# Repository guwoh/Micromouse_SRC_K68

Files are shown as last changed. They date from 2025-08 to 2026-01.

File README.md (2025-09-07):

# Micromouse_SRC_K68
# Welcome

BOM list: https://docs.google.com/spreadsheets/d/1yc7NAcJtB-HrwJn92QKEUpOmXSOkb5Ers7y2r0_20j4/edit?usp=sharing

//////////

Khung xe:

Tham khảo 1 http://greenye.net/Pages/Micromouse/Futura.htm Tham khảo 2 https://github.com/ukmars/ukmarsbot Tham khảo 3 https://contest.techbriefs.com/2023/entries/robotics-and-automation/12536 Tham khảo 4 https://kswichit.net/micromouse/micromouse.html

/////////////////

VL53l0x lazer sensor connection: https://copilot.microsoft.com/sl/jY64h9Ku57s https://github.com/pololu/vl53l0x-arduino https://learn.adafruit.com/adafruit-vl53l0x-micro-lidar-distance-sensor-breakout/arduino-code

////////////////

Motor driver https://learn.adafruit.com/adafruit-drv8833-dc-stepper-motor-driver-breakout-board/overview

//////////

MPU6050 https://microcontrollerslab.com/micropython-mpu-6050-esp32-esp8266/ http://community.heltec.cn/t/problem-using-mpu-6050-accel-gyro-with-wifikit-esp32-board/2227/8

ESP32 pinout: https://lastminuteengineers.com/handling-esp32-gpio-interrupts-tutorial/ https://lastminuteengineers.com/esp32-pinout-reference/

Kalman Filter: https://www.kalmanfilter.net/alphabeta.html

test merge

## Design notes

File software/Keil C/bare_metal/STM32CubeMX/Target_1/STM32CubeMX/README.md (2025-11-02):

1. 📚 Phần khai báo (Ở đầu file)
/* USER CODE BEGIN Includes */

Chức năng: Nơi để bạn thêm các lệnh #include của riêng mình.

Ví dụ: #include "my_gpio_driver.h"

/* USER CODE BEGIN PTD */ (Private TypeDef)

Chức năng: Nơi để định nghĩa các typedef (struct, enum) của riêng bạn.

Ví dụ: typedef struct { ... } SensorData_t;

/* USER CODE BEGIN PD */ (Private Define)

Chức năng: Nơi để thêm các lệnh #define hằng số.

Ví dụ: #define LED_PIN 5

/* USER CODE BEGIN PV */ (Private Variables)

Chức năng: Nơi để khai báo các biến toàn cục (global variables).

Ví dụ: uint32_t g_tick_count = 0;

/* USER CODE BEGIN PFP */ (Private Function Prototypes)

Chức năng: Nơi khai báo "prototype" (nguyên mẫu hàm) cho các hàm bạn tự viết.

Ví dụ: void My_Clock_Init(void);

/* USER CODE BEGIN 0 */

Chức năng: Nơi để viết các hàm (ví dụ: hàm xử lý ngắt SysTick_Handler) trước hàm main().

2. ⚙️ Bên trong hàm main()
/* USER CODE BEGIN 1 */

Chức năng: Nơi để code chạy ngay khi vào main().

Vị trí VÀNG cho code bare-metal: Đây là nơi hoàn hảo để bạn đặt hàm khởi tạo clock (RCC) của mình.

/* USER CODE BEGIN Init */ & /* USER CODE BEGIN SysInit */

Chức năng: Dùng để khởi tạo các thành phần hệ thống khác. Bạn có thể đặt hàm khởi tạo Systick của mình ở đây.

/* USER CODE BEGIN 2 */

Chức năng: Nơi để code khởi tạo trước vòng lặp while(1).

Vị trí VÀNG cho code bare-metal: Đây là nơi hoàn hảo để bạn đặt hàm khởi tạo ngoại vi (GPIO, UART, Timers...) sau khi clock đã chạy ổn định.

/* USER CODE BEGIN 3 */

Chức năng: Nơi chứa code logic chính của bạn.

Vị trí VÀNG cho code bare-metal: Code của bạn trong vòng lặp while(1) sẽ được đặt ở đây.

3. 📝 Phần định nghĩa hàm (Ở cuối file)
/* USER CODE BEGIN 4 */

Chức năng: Nơi để viết nội dung/định nghĩa cho các hàm mà bạn đã khai báo ở PFP.

Ví dụ:

C

void My_Clock_Init(void)
{
  // Code RCC bare-metal của bạn
}

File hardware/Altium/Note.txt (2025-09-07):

- dong co se duoc lam cao len 2mm
- tìm mt6701 và do chan nam cham, ròi v3 3d
- phần 3d nam châm làm sau

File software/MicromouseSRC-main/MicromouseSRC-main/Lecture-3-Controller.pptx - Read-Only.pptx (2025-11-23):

## Lecture 3: The Controller

PID Control and Speed Profile

## Objective (to be completed over the next 2-3 weeks)

- Create a system that allows you to easily control the angular and translational velocity of your mouse
- Utilize feedback from multiple sensors (IR sensors, encoders, gyro)
- Mouse should accelerate and decelerate at a constant rate, for both angular and translational movement
- Mouse should not collide with walls
- Control your mouse using practical measurement units, like millimeters

## Overview

- Most of the code will be in the systick handler
  - This will make sure that your mouse is always maintaining the correct velocity
  - Also makes sure we can obtain accurate velocities, since we know the time between systick calls (1 ms).
- From outside your controller, you will be able to set the mouse’s two velocities (angular and translational). The controller will automatically accelerate or decelerate to that velocity, then maintain it.

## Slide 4

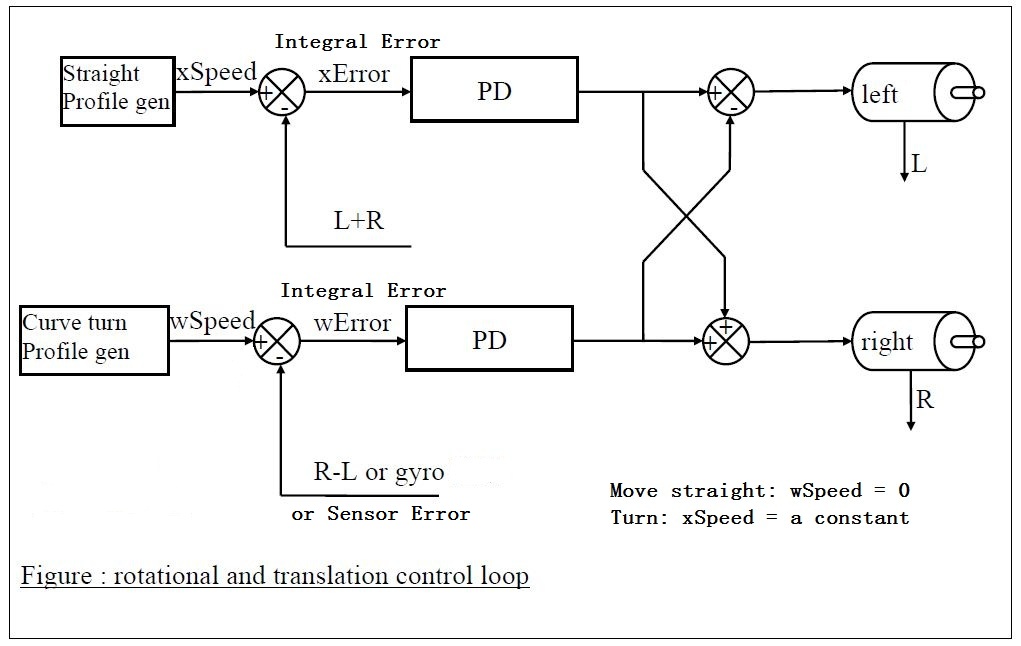
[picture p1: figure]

## Speed Profile

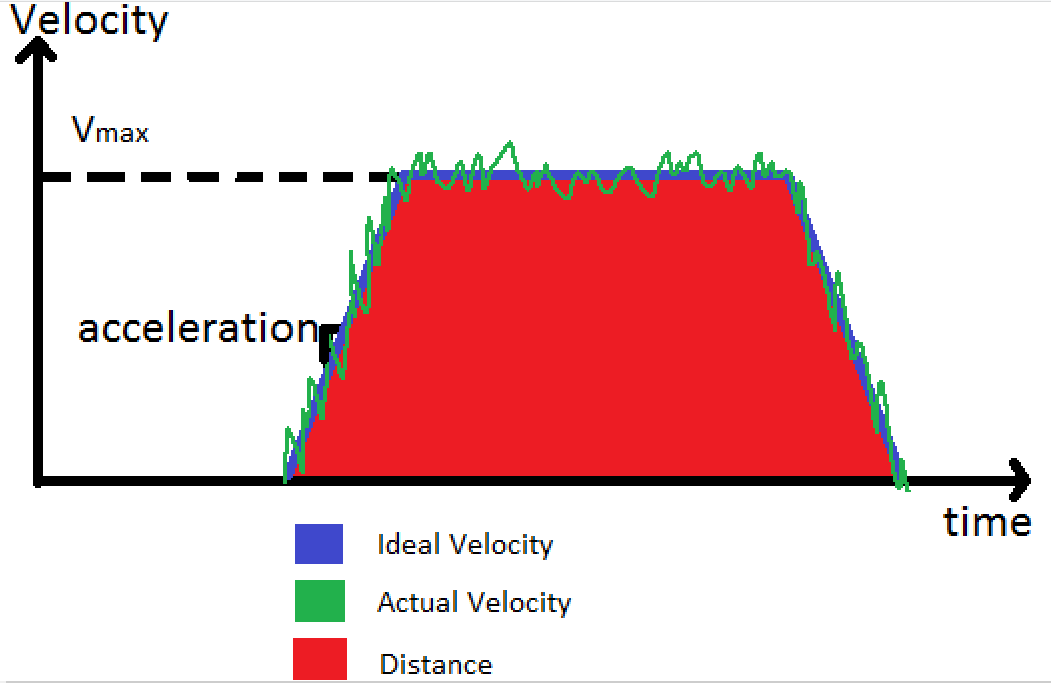
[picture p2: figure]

## The Steps

Within 1ms we need to finish all things as follow in sequence
1. Collect data from all Sensors(IR, gyro, encoders)
2. Decide the ideal velocities you want
3. Find the actual velocities from sensors as feedback(encoder value for translational velocity and gyro for rotational velocity)
4. Find difference between ideal velocity and feedback as Error
5. Input errors to PD controller in a clever way
6. Set the PWM of the motors based on the output from PD controller

## Find the actual velocities

- Take the derivative of the encoder counts
- Gyro also gives you the angular velocity

## Find the ideal velocities

- If you are accelerating or decelerating, then add or subtract (respectively) your acceleration rate from the previous ideal velocity to get the current ideal velocity
- If you are not accelerating or decelerating, then your current ideal velocity is unchanged
- This creates the ideal trapezoidal shape for your speed profile

## Get the PID input

- For translational:
  - We really only have encoders for feedback, since the gyro doesn’t tell us translational movement and the front sensors don’t have a wall close enough most of the time
  - Therefore we can use the ideal velocity minus the actual velocity for our PID input
- For angular:
  - Same as the translational, but we can add sensor error and gyro error.
    - You will need to scale the gyro output so that has roughly the same value as the encoder error
    - Note that the sensor error is a positional error, while the encoder and gyro errors are velocities

## Apply PID to errors

- The velocity error is already your D (remember we took the derivative of the encoder count at the beginning)
- Integrate the velocity error to obtain P.
- Essentially what we want is a “Positional PD Controller”.
- However, we also want to use PI for our sensor error.
  - Integrating the sensor error allows us to permanently correct our angle if the angle of our mouse is off.
- Using a PI controller for our encoder velocity error, gyro error, and (positional) sensor error will give us everything we want.

## Set the PWM of the motors

- Something like this should be at the end of your systick function:
setLeftPwm(errorX – errorW);
setRightPwm(errorX + errorW);
- errorX is the translational error
- errorW is the angular error
- You can change the direction of errorW if you want, just switch the + and -

## Get sensor error

if(DLSensor > DLMiddleValue && DRSensor < DRMiddleValue)
sensorError = DLMiddleValue - DLSensor;
else if(DRSensor > DRMiddleValue && DLSensor < DLMiddleValue)
sensorError = DRSensor - DRMiddleValue;
else
sensorError = 0;

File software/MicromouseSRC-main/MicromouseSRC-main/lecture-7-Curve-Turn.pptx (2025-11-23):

## Lecture 7 Curve Turn

## Basic Concepts

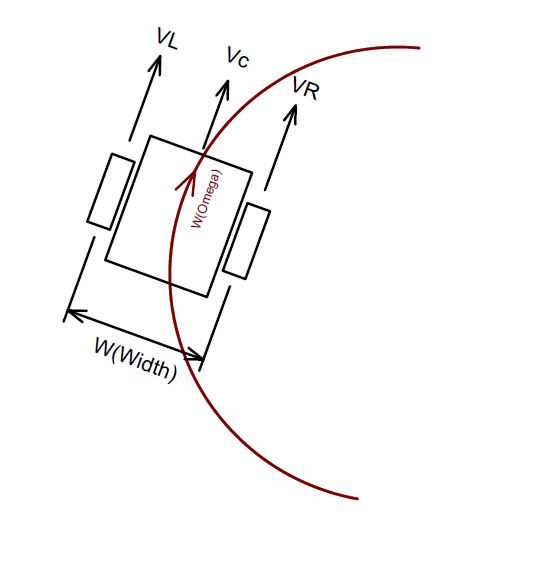
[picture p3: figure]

- Keep speed with certain ratio between 2 wheels for mouse to make mouse turn at certain angular velocity
- However this is not possible in real word
- When on straight, VLs=VRs
- When turn VLt>VRt
- Motor can’t suddenly change speed from VLs to VLt, and VRs to VRt

## Diagram view

This is not possible in real world!

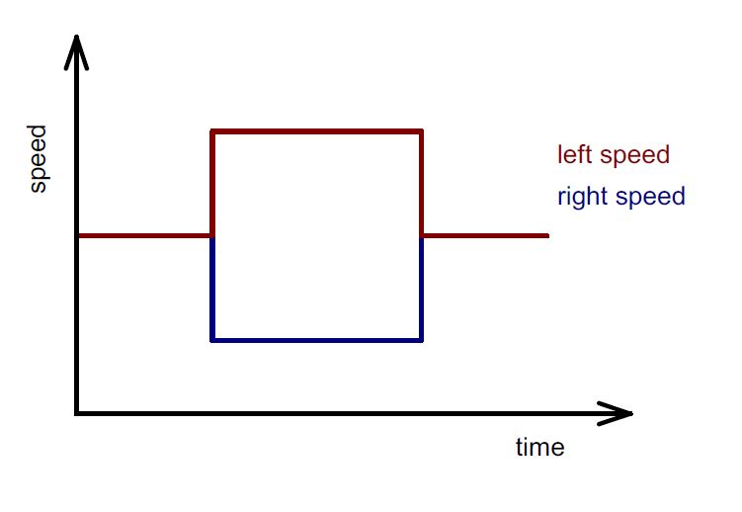
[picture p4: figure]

## Alternative solution

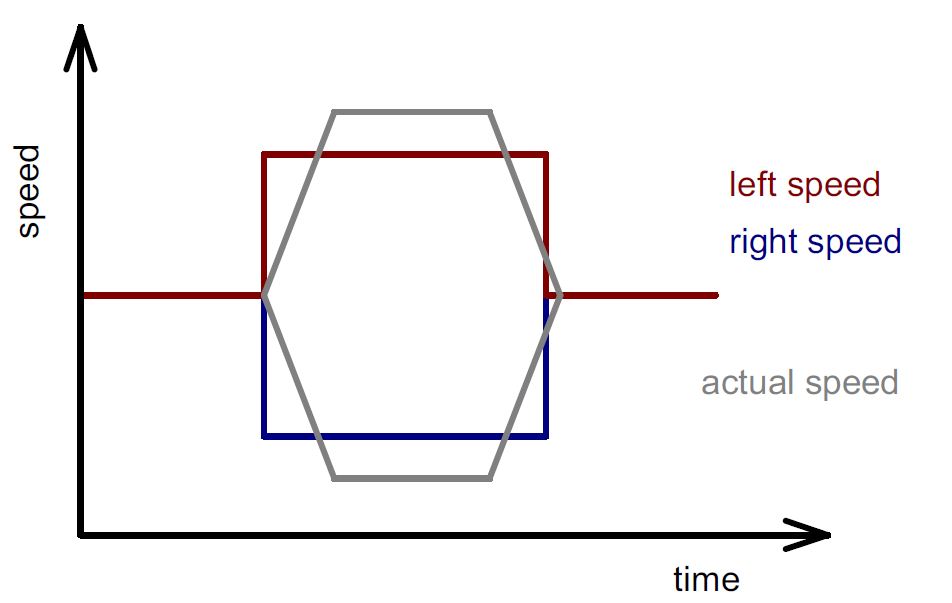
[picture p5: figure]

Make one wheel accelerate, the other wheel decelerate to reach different speed gradually

## How to maintain same turn angle in this way?

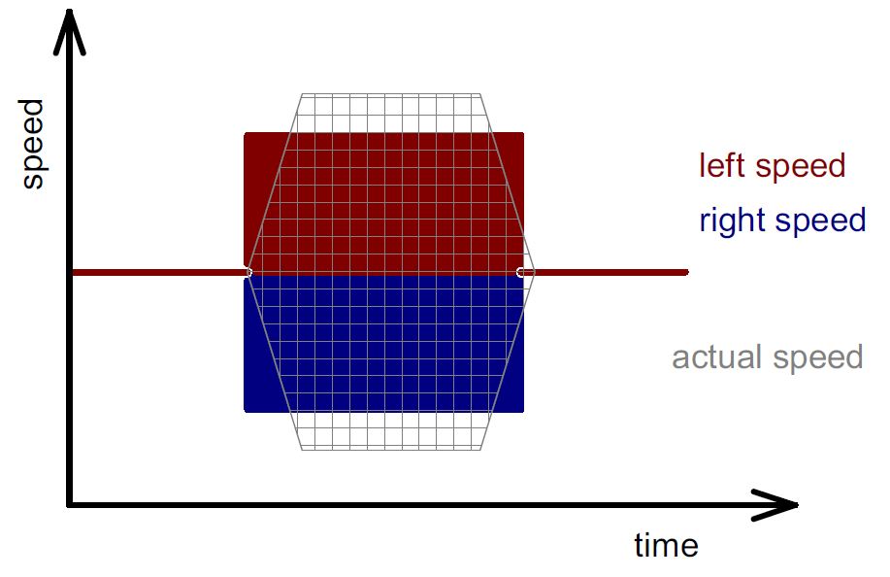
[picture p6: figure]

- All you need to do is just to keep the grey area equals to the sum of red and blue area to maintain the same turning angle

## Some facts

- The center speed of mouse remains constant when turning since VC = (VL + VR)/2
- VR – VL is still the rotational feedback when turning
- You can use the feedback from gyro to replace VR-VL to prevent slippage, however needs to be scale to fit the system with encoder ticks

## The view of angular velocity

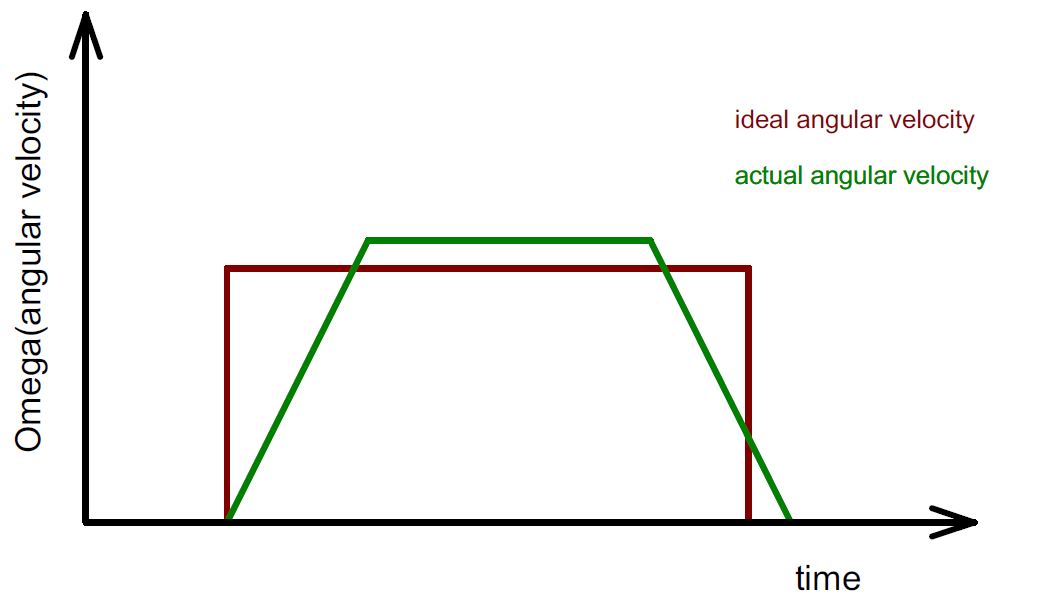
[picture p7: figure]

- W(omega) = VR – VL in our system
- Diagram in angular velocity form is more straight forward since the center linear velocity of mouse doesn’t change during the turn

## Keep the area same

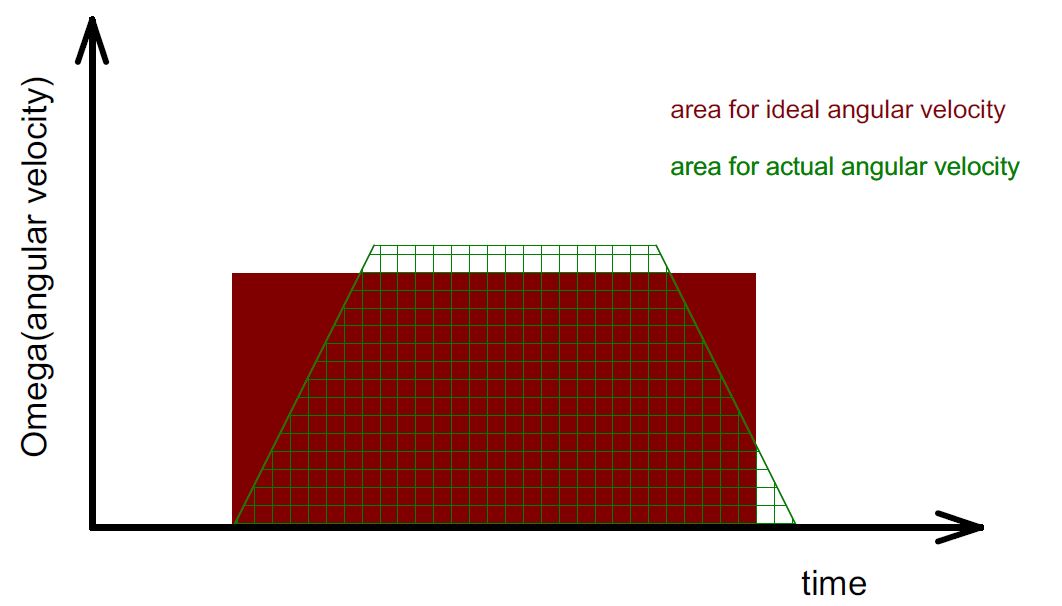
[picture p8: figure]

- As long you keep the area same between ideal and actual angular velocity, the mouse will turn with same angle you desired
- Some extra time is usually needed for actual turn

## How to design your profile?

- Decide the max angular velocity W(omega)
- Decide the angular acceleration (alpha)
- Calculate the area for idea turn, make the actual turn area equals to it
- Use matlab, excel to make your profile, and keep track of the position of the mouse at each millisecond, keep adjusting the input parameters, until the actual output curve for mouse exits at same location with idea curve
- Apply the parameter decided from simulation profile to your mouse

## An example with excel

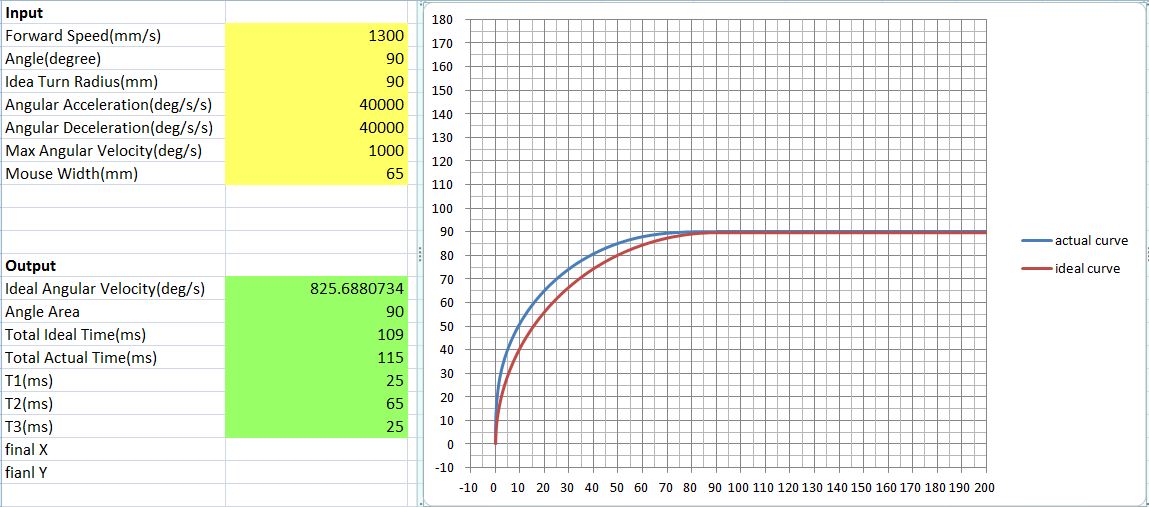
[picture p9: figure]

## Demo with the simulation profile

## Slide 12

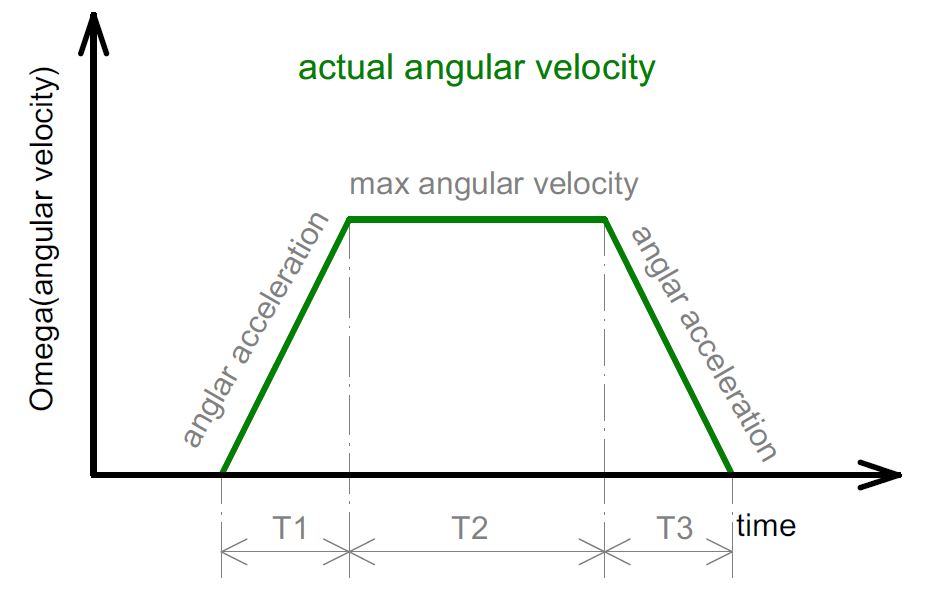
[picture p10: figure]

## How to make it work on mouse?

- Center forward linear velocity, turn angle, angular acceleration, max angular velocity are all know in this case.
- Assume T1 = T3 to simplify the case where the slope(angular acceleration rate) are same
- Calculate the corresponding angular velocity with T1, slope or max angular velocity at T1 and T3
- The angular velocity is max angular velocity at T2

## Sample code

- Having this is your controller:
- If currentSpeedW < targetSpeedW
{
currentSpeedW += accW
if currentSpeedW > targetSpeedW
currentSpeedW = targetSpeedW
}
else If currentSpeedW > targetSpeedW
{
currentSpeedW -= accW
if currentSpeedW < targetSpeedW
currentSpeedW = targetSpeedW
}

## Sample cont.

- The code for your turn function
- Void turn(void)
{
if(is at T1 or T2)
targetSpeedW = maxAngularVelocity;
else if(is at T3)
targetSpeedW = 0;
}

## Things need to know

- The angular velocity has different sign between left turn and right turn
- Record the system time in millisecond to keep track of you current time for curve turn.
- The angular velocity you generate from provided excel profile generator is in degree/s unit, you need to convert to recognizable unit of mouse

## Unit conversion for speed profile

- Angular velocity in encoder format equals to:
wheelDistance*angularVelocity*Pi*oneCellDistance/cellLength/180/1000
- Where
- wheelDistance is distance between centers of the wheels
- angularVelocity is the angular velocity in degree/s
- OneCellDistance is the encoder counts per cell for one wheel
- CellLength is the length of each cell, which is 180mm
- /180 is divide 180 degree
- /1000 converts from /s to /ms

## How to convert for gyro feedback

- The intermediate unit between gyro and encoder is distance(meter)
- Use pivot turn method to make conversion, where VL = -VR
- Record the angle output from gyro when make a 180 degree turn(either directions), as “a”
- Get distance value of
- 2*Pi*R which is Pi*W in SI unit then convert to encoder counts, as “b”

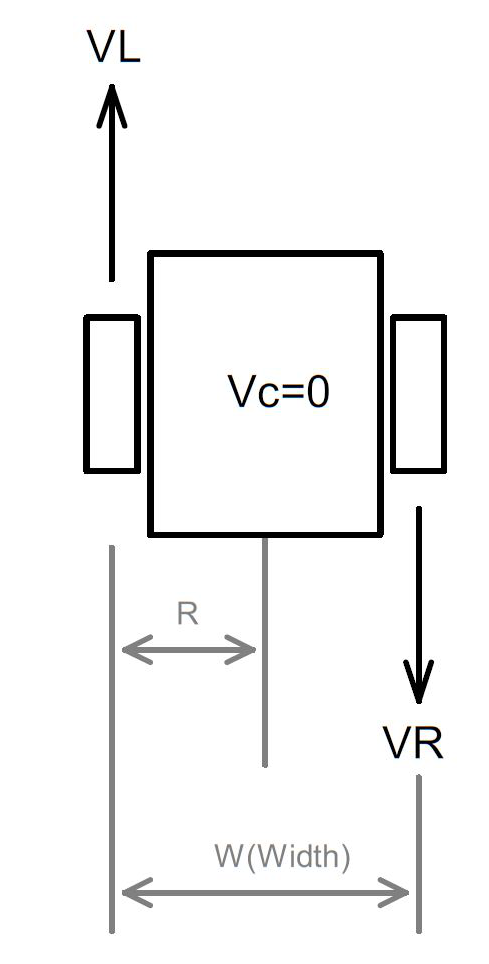
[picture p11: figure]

## Unit Conversion (cont.)

- You get the ratio between b and a as “Ratio” = a/b (usually a > b)
- Now you can apply the ratio to the angular velocity read from gyro and have it easily convert to encoder format:
angularFeedback = aSpeed/Ratio
angularFeedback also equals VR-VL by definition in controller lecture
- Now you can only use gyro as rotational feedback for curve turn

## Question?

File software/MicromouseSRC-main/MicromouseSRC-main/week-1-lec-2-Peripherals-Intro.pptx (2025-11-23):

## Lecture 2

Peripharals Hardware Introduction

## IR Emitter Single

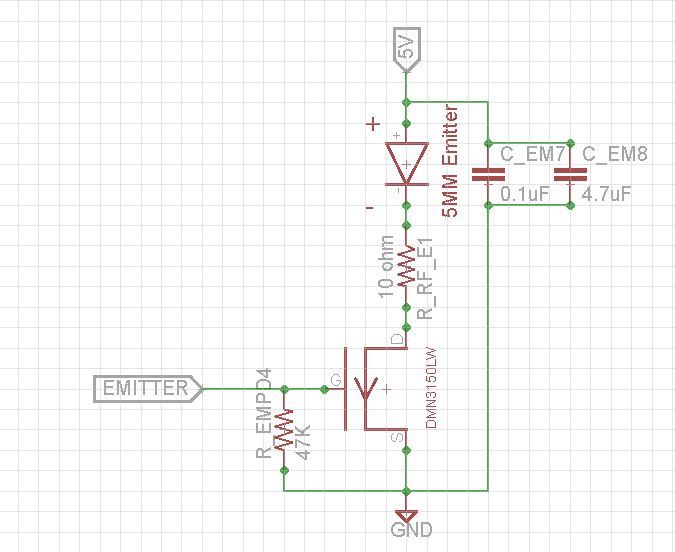
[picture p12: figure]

## Emitter Serial

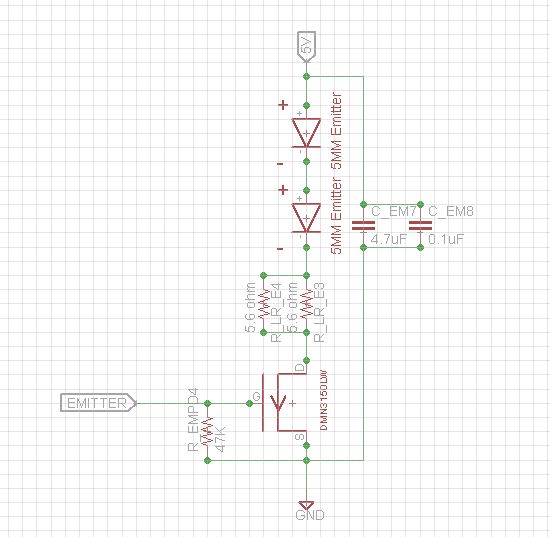
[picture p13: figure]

## IR Receiver

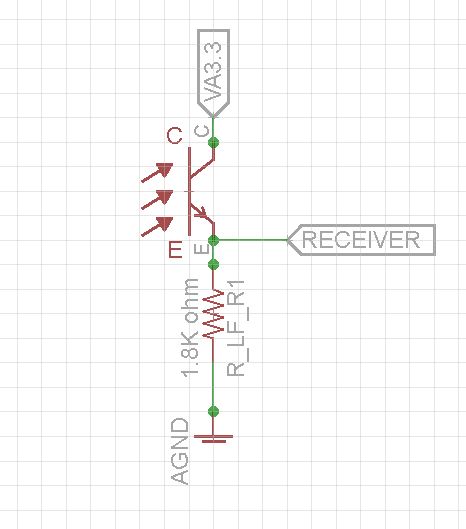
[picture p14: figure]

## IR Sensor Pulsing Timing

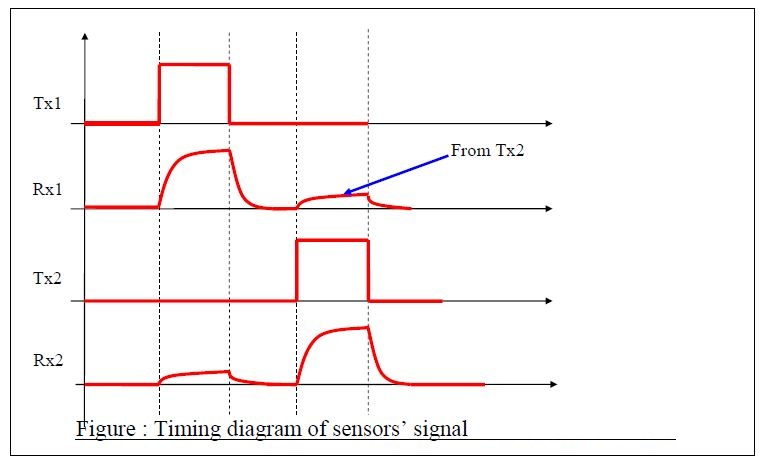
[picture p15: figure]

Delay between each sensor reading until all residues are gone

## Gyro

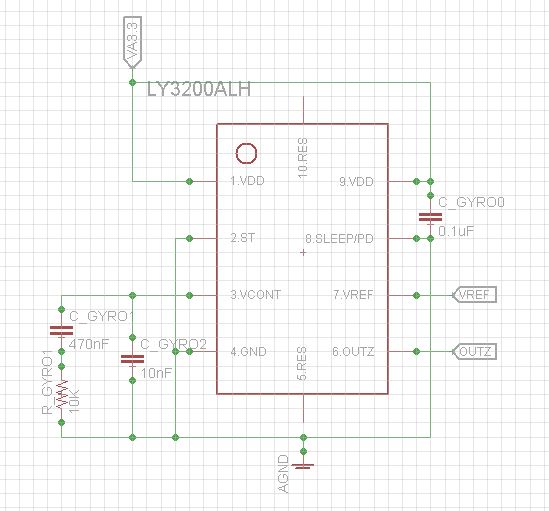
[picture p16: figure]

## Gyro Zero Point Drift

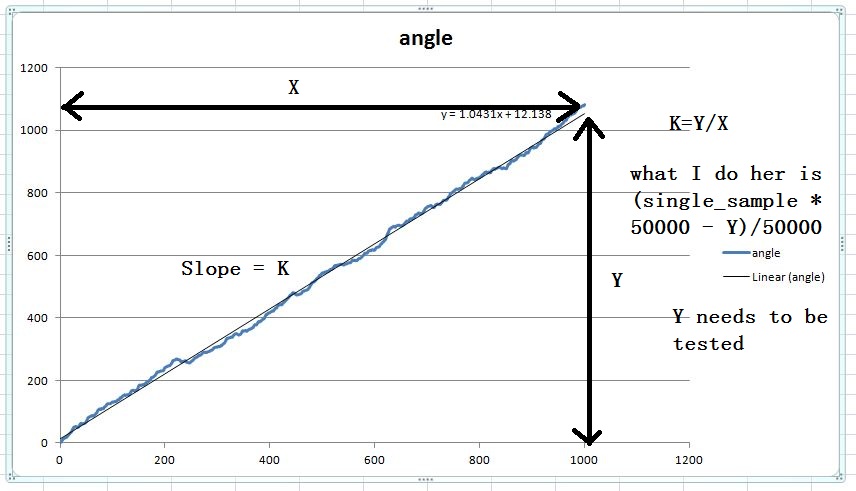
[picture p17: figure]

The accumulated angled when mouse is mouse moving with gyro zero point drifting is increased linearly

## Buzzer

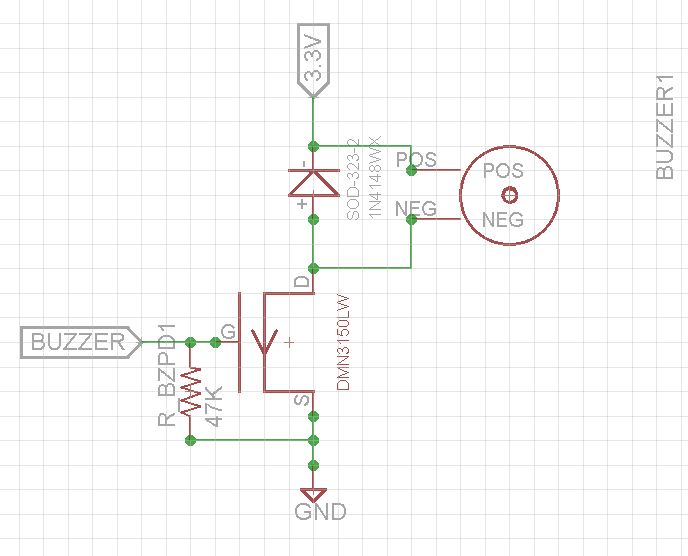
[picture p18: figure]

## Display

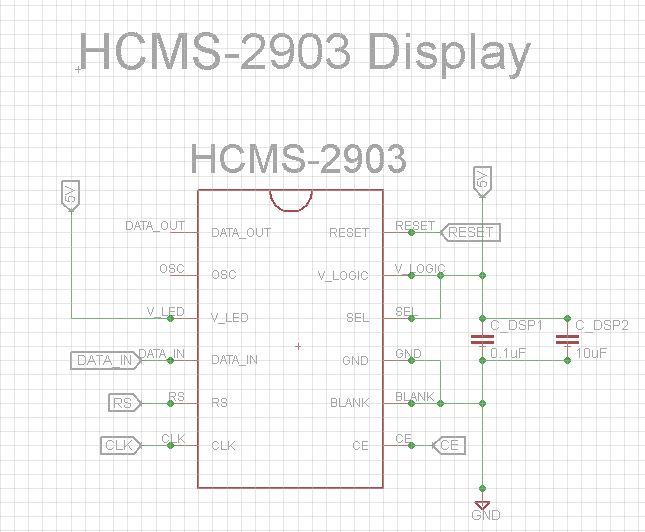
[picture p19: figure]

## Motor Driver

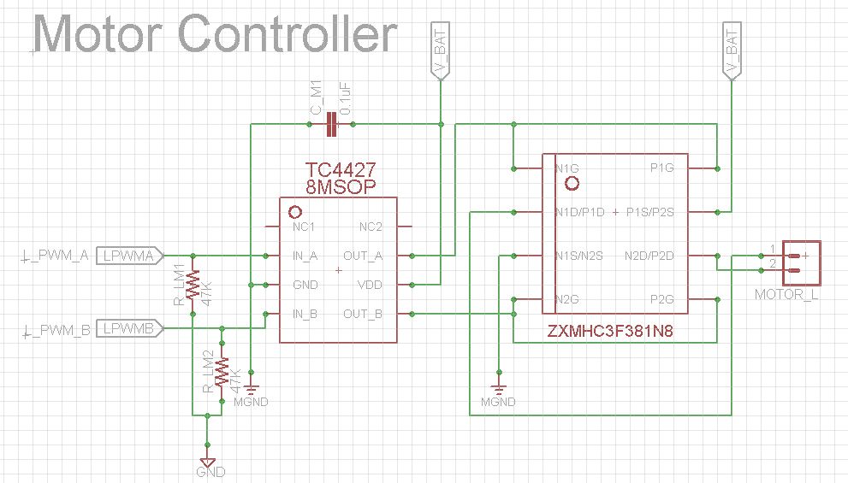
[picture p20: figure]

## Voltage Meter

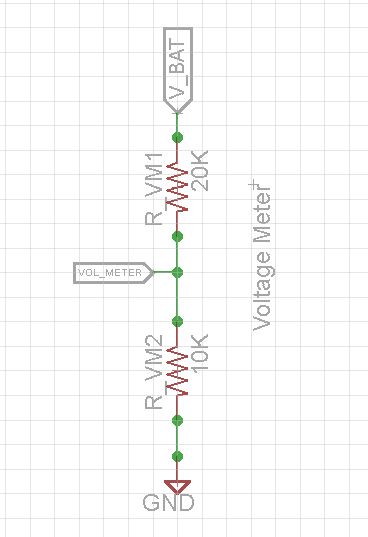
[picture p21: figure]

Keep track of the battery voltage to protect the batter from over discharging

## Power V_bat

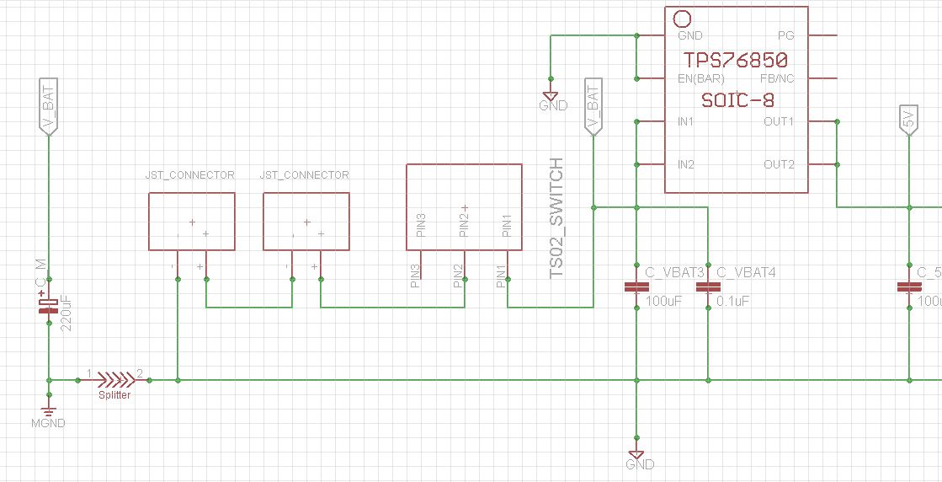
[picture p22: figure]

## Power 5V

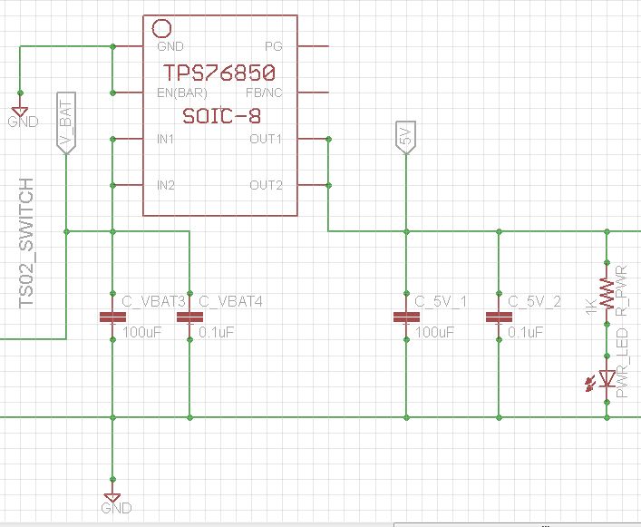
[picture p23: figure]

## Power 3.3V

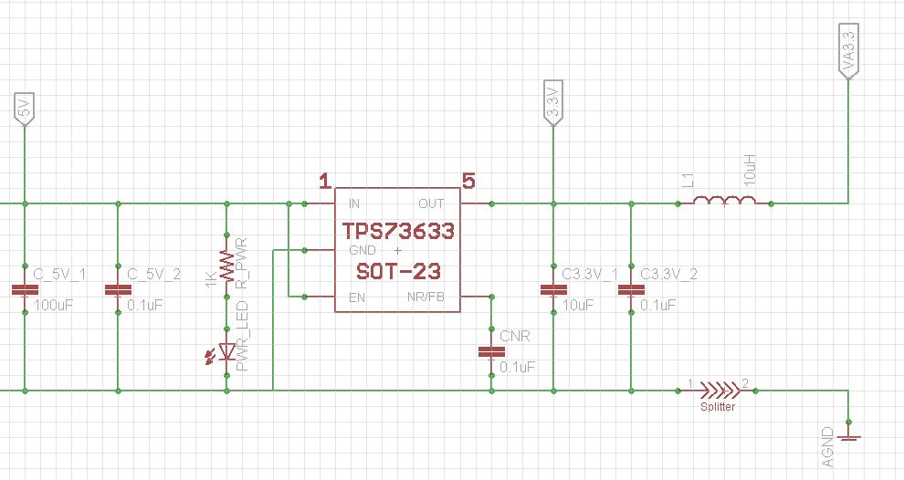
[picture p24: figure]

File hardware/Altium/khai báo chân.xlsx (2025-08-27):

Số thứ tự | Tên chân | Chức năng | Column1
1 | VBAT | 33
2 | PC13/RTC_OUT
3 | PC14/OSC32_IN
4 | PC15/OSC32_OUT
5 | PH0/OSC_IN | kết nối với thạch anh |  | Đã dùng
6 | PH1/OSC_OUT | kết nối với thạch anh |  | Không dùng
7 | NRST | reset | buzzer | Chưa dùng
8 | PC0 | ir thu left | 8 con debug led
9 | PC1 | ir thu right | ir phát ir thu
10 | PC2/SPI2_MISO | ir thu f_left
11 | PC3/SPI2_MOSI | ir thu f_right
12 | PA0/WKUP
13 | PA1/USART2_RTS | IN1: điều khiển động cơ
14 | PA2/USART2_TX | IN2: điều khiển động cơ
15 | PA3/USART2_RX | IN3: điều khiển động cơ
16 | VDDA | 33
17 | VSS | GND
18 | PA4 | IN4: điều khiển động cơ
19 | PA5/SPI1_SCK | DB LED
20 | PA6/SPI1_MISO
21 | PA7/SPI1_MOSI
22 | PC4
23 | PC5
24 | PB0
25 | PB1
26 | VCAP_1 | 33
27 | VCAP_2 | 33
28 | PC6
29 | PC7
30 | PC8
31 | PC9
32 | PA8
33 | PA9 | TX
34 | PA10 | RX
35 | PA11
36 | PA12
37 | PA13/JMS-SWDIO | SWDIO
38 | VSS | GND
39 | VDD | 33
40 | PA14/JTCK-SWCLK | SWCLK
41 | PA15
42 | PC10
43 | PC11
44 | PC12
45 | PB2 | BOOOT1
46 | VDD | 33
47 | VSS | GND
48 | PB3
49 | PB4
50 | PB5 | BUZZER
51 | PB6 | SCL
52 | PB7 | SDA
53 | BOOT0 | BOOT0
54 | PB8 | DBL_1
55 | PB9 | DBL_2
56 | PB10 | DBL_3
57 | PB11 | DBL_4
58 | VSSA | GND
59 | VDD | 33
60 | PB12 | DBL_5
61 | PB13 | DBL_6
62 | PB14 | DBL_7
63 | PB15 | DBL_8
64 | VDD | 33
65 | PB1 | IRP MPU
67 | PB0

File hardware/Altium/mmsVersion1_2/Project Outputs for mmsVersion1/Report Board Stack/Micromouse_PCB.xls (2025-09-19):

Board Stack Report
Stack Up |  | Layer Stack
Layer | Board Layer Stack | Name | Material | Thickness | Constant
1 |  | Top Overlay |  | 0mil
2 |  | Top Solder | Solder Resist | 0.4mil | 3.5
3 |  | Top Layer |  | 1.4mil
4 |  | Dielectric 1 | FR-4 | 12.6mil | 4.8
5 |  | Bottom Layer |  | 1.4mil
6 |  | Bottom Solder | Solder Resist | 0.4mil | 3.5
7 |  | Bottom Overlay |  | 0mil
 | Height : 16.2mil

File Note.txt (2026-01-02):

- Bỏ cuộn cảm ở MCU
- Chưa cấp nguồn cho bmg250
- Xem lại VDDA (hình như VDDA chưa nối với v33 nào)
- Chỉnh lại một số linh kiện về 0603 hoặc 0805
- Thay đổi sang thạch anh nhỏ hơn

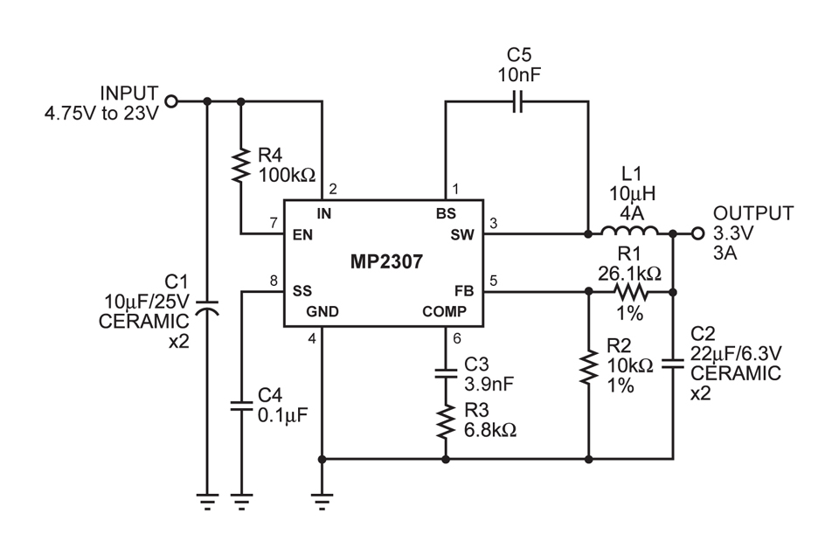
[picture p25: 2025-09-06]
Documents/Monolithic_Power_Systems-MP2307DN-LF-image.jpg

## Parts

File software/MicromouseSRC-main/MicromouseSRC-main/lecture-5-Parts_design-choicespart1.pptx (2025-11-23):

## Lecture 5 Parts/design Choices (Part 1)

## IR Sensor

- Consists of IR LED(transmitter/emitter) and IR receiver(transistor type most likely)
- Wavelengths much match between emitter and receiver
- Pulsing high current to raise Signal/Noise ratio
- Use voltage divider for receiver converting current signal to voltage signal

## Specs for IR Emitter

- Specs need to know when choosing an IR Emitter:
1. Wavelength
2. Voltage drop
3. DC Forward current
4. Pulsing current/timing
5. Viewing angle(full angle)
6. Radiant Intensity

## Wavelength

- 950nm and 850nm are the 2 most popular choices for IR emitter
- You need to find IR receive that matches the wavelength of emitter in order to max power efficiency

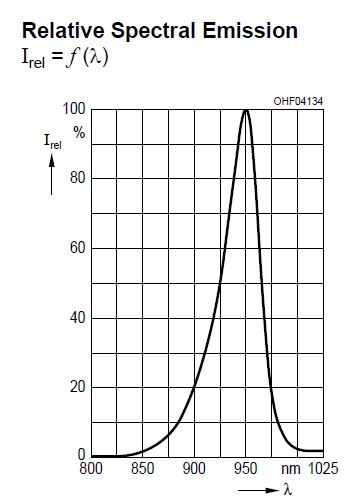
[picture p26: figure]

## Voltage Drop

- IR Emitter is essentially an LED that emits infrared
- And LED is essentially an diode, and diode drops voltage
- Voltage drop varies depends of the expected current
- Examples:
- SFH4550 drops 1.5V @100mah
- SFH4545 drops 1.5V @100mah
- SFH4511 drops 1.3V @ 100mah(discontinued)

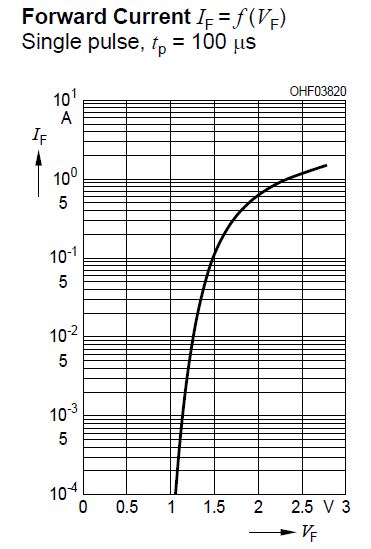
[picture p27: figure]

## DC Forward Current

- Means the max constant current that the IR emitter can safely handle(max limit)
- Usually 100mah for typical 5mm diameter IR LED, 50mah for 3mm diameter IR LED. Some metal shield package version has even higher DC forward current
- DC forward current somehow indicates the capability of IR Emitter when pulsing at high current

## Pulsing Current

- LED allows pulsing current higher than DC forward current during a short time period
- Max Capability are different at different turn on time
- Exceeding max cap will damage the IR LED
- Should always check table to ensure your time/current choice for your design

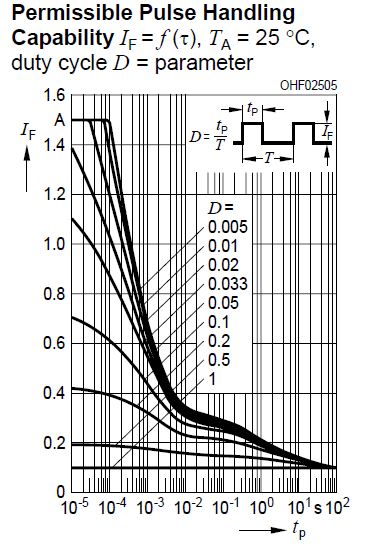
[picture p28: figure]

## Viewing angle

- Smaller angle is preferred for higher power intensity and more accurate distance detect, usually under 10 degree

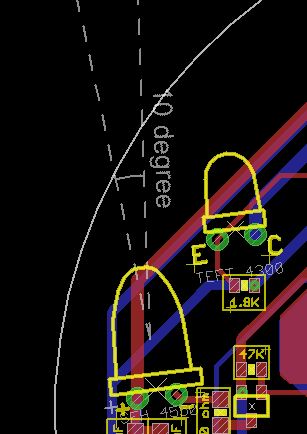
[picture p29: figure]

Chip position indicates where the IR light starts to emit

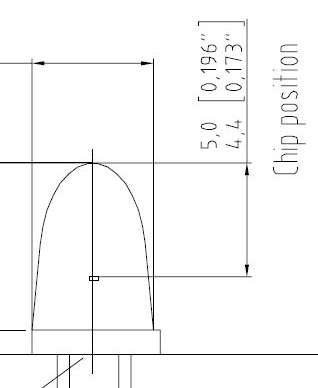
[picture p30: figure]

## Radiant Intensity

- Indicates the power intensity per unit area
- Varies between different models
- The higher the better
- 850nm type has higher Intensity than 950nm in general
- Example:
- SFH4550(850nm)6degree 630mW/sr @ 100mA
- SFH4545(950nm)10degree 550mW/sr @ 100mA
- SFH4511(940nm)8degree 63mW/sr @ 100mA(discontinued)

## Some other important facts

- Package:
- T 1 ¾ is about 5mm diameter package
- T1 is about 3mm diameter package
- Through hole preferred for the availability and efforts on mounting it on the mouse
- Choices are pretty obvious when you use the filter on vendor’s site(ie. Mouser,digikey, etc) when you apply the preferred specs

## IR Receiver

- Viewing angles are always wider than emitter
- Angles are between 30-60 degree
- Receiver has sensitive wavelength range, as long as it covers the wavelength for IR emitter
- The resistance of the resistor that serial with is based on your own test and preference. Resistance value will affect the max reading value and receiver charge/discharge time
- Faster charging time saves pulsing time but could be too sensitive, slower charging time takes more time but less sensitive(less sensitive for ambient noise)

## Matching wavelength

Emitter(SFH4545) Receiver(TEFT4300)

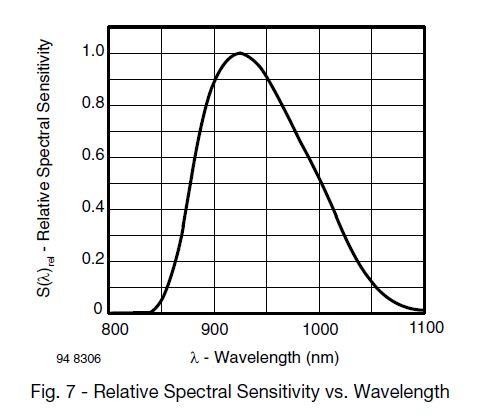
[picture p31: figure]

## Circuit example

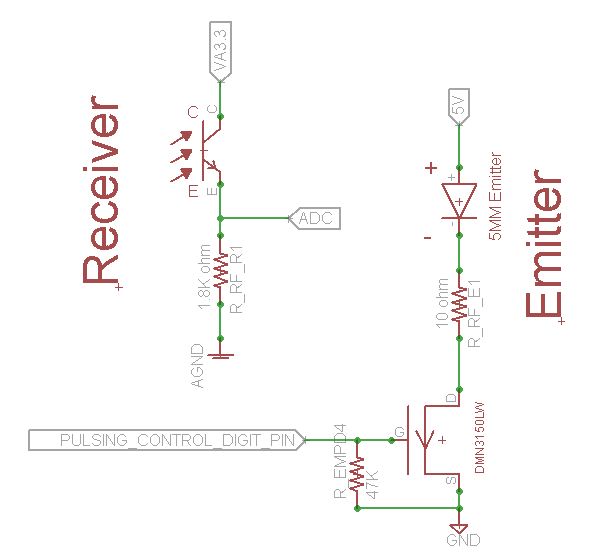
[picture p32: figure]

## Power Supply

- Use 2 lipo Batteries serial at 7.4V at V_bat
- Use 2mm pitch JST male plug mount on PCB
- 2.54mm or 2mm pitch slide switches are usually used, pay attention with power rating
- Large value tantalum capacitors are used to stabilized the power supply, pay attention of the max voltage and ESR(equivalent serial resistance) of tantalum capacitor

## Power Supply(cont.)

- 3 different voltage usage in system
- v_bat for motor driver and voltage meter
- 5V for IR emitter and encoder power supply
- 3.3V for rest of the sytem
- Current consumption level
- Motor(V_bat)>5V(emitter)>3.3V
- Choice on Futura Kit Mouse
- 5V LVO regulator with 1A max output
- 3.3V LVO regulator with 400mah max output
- Sufficient current with the regulator chosen above
- The voltage drop for LVO regulator is as low as possible(especially for 5V regulator)

## Power Supply(digital)

- Add by pass cap before and after to stabilize supply
- Add low pass cap before and after to filter out high freq. noise

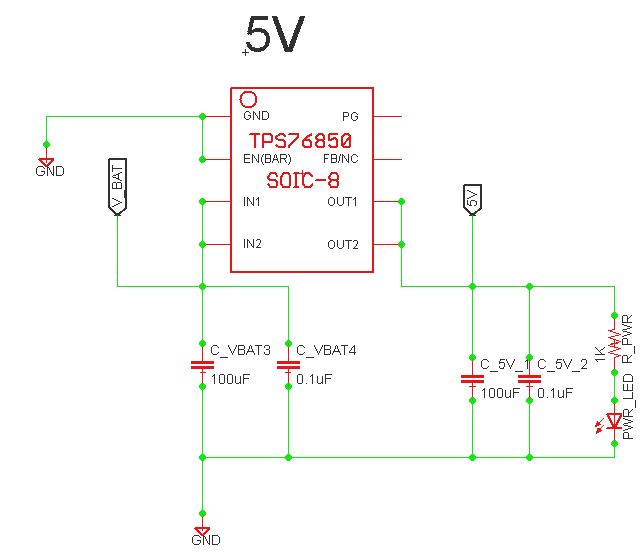
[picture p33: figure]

## Power Supply(analog)

- Separate ground is preferred to reduce the noise to analog device
- Usually serial a inductor between supply and analog supply to stabilized the analog power supply


## Power Supply(motor)


- Tantalum cap to supply motor power(place very close to motor driver)
- Low pass filtering cap very close to motor driver
- Separate ground for motor


## RCL selection

- Smaller package leaves you more space on mouse, harder to solder, and higher ESR
- Package on Futura Kit Mouse:
- 0603 resistor for IR Emitter(250mw rating, because of high current)
- 0402 resistor for rest of the system
- 1220(in) tantalum cap for 100uF 2917(in) tantalum cap for 220uF(motor supply)
- 0603 caps for rest of the system
- 1007 10uF Inductor
- RCL availability in lab
- 0402 resistor stocked for all value you need for micromouse
- 0603 capacitor stocked for all value you need for micromouse
Pay attention of the max voltage of the cap and power rating for resistor

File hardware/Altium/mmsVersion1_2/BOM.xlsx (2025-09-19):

Comment | Description | Designator | Footprint | LibRef | Quantity
100K | RES Thick Film, 2.49Ω, 1%, 0.125W, 200ppm/°C, 0805 | 3 | FP-CRCW0805-e3-IPC_B | CMP-02407-004732-1 | 1
 | FSMSM Push Button Switch, 50 mA, -35 to 85 degC, 2-Pin SMD, RoHS, Tape and Reel | BOOT0, DEBUG, RST | TECO-FSMSMTR_V | CMP-2000-07501-1 | 3
22pF | Cap Ceramic 22uF 6.3V X7R ±20% SMD 1210 +125°C Embossed T/R | C1, C2 | FP-CL32-IPC_B | CMP-13271-001877-1 | 2
105 | CL21 Series 0805 1uF 25V -20/+80% Tolerance Y5V Multilayer Ceramic Chip Capacitor | C3 | FP-CL21-IPC_B | CMP-13271-002018-1 | 1
2.2uF | CL21 Series 0805 2.2uF 16V -20/+80% Tolerance Y5V Multilayer Ceramic Chip Capacitor | C4, C5 | FP-CL21-IPC_B | CMP-13271-004097-1 | 2
100nF | Cap Ceramic 100nF 25V X7R ±10% Pad SMD 0603 +125°C T/R | C6, C7, C8, C9, C10, C_DB, C_IR2, C_IR4 | FP-CL10-IPC_C | CMP-13271-001423-1 | 8
4.7 uF | 4.7uF 20V ±10% 4Ω 3216(mm) SMD Tantalum Capacitor | C11, C27 | FP-TAJA-MFG | CMP-04424-000323-2 | 2
10uF | C1206 10 uF C0G 5.00% 50 V | C12 | FP-C1206C-EB-MFG | CMP-1037-00646-2 | 1
0.1uF | C1206 10 pF C0G 5.00% 50 V | C13, C_enA, C_enB | FP-C1206C-EB-MFG | CMP-1037-00646-2 | 3
3.9nF | C1206 4.8nF C0G 5.00% 50 V | C14 | FP-C1206C-EB-MFG | CMP-1037-00646-2 | 1
10nF | C1206 10 pF C0G 5.00% 50 V | C15 | FP-C1206C-EB-MFG | CMP-1037-00646-2 | 1
22uF | C1206 10 pF C0G 5.00% 50 V | C16 | FP-C1206C-EB-MFG | CMP-1037-00646-2 | 1
106 | Multi-Layer Ceramic Capacitor 10uF 50V X5R ±10% 1206 Emboss T/R | C17, C18, C23, C24 | FP-GRT31C-0_2-IPC_A | CMP-06035-000076-2 | 4
106 | CAP TANT 10UF 10% 25V 2312 | C19 | FP-T491C-MFG | CMP-03017-000001-1 | 1
103 |  | C20 | CAPC2013X88X50LL20T25 | CMP-2007-00266-1 | 1
225 | Chip Capacitor, 2.2 uF, +/- 10%, 50 V, -55 to 125 degC, 1206 (3216 Metric), RoHS, Tape and Reel | C21 | CAPC3216X180X50LL20T25 | CMP-1037-04831-2 | 1
10nF | Cap Ceramic 100nF 25V X7R ±10% Pad SMD 0603 +125°C T/R | C22 | FP-CL10-IPC_C | CMP-13271-001423-1 | 1
Capacitor 4.7µF +/-40% 25V 0805 | Chip Capacitor, 4.7µF +/-40%, 25V, 0805, Thickness 1.45 mm | C_IR1, C_IR3 | CAPC0805(2012)145_L | CMP-001-00080-4 | 2
RED | LED GREEN CLEAR CHIP SMD | D1, D3, D5, D6, D7, D8, D9, D10, D11, D12, D13 | FP-LTST-C190GKT-MFG | CMP-22017-000005-2 | 11
MMSZ5232B | MMSZ5232B MMSZ523 Series 500 mW 5.6 V 10 mA SMT Half-Watt Zener Diode SOD-123 | D4 | FP-MA02A-MFG | CMP-00278-11829623-1 | 1
Resistor 1k +/-1% 0805 125 mW | Chip Resistor, 1 KOhm, +/- 1%, 0.125 W, -55 to 155 degC, 0805 (2013 Metric) | DBL_1, DBL_2, DBL_3, DBL_4, DBL_5, DBL_6, DBL_7, DBL_8 | RESC2013X70X40ML20T20 | CMP-009-00010-5 | 8
IR RECV | TSFF5210 TSFF5210 IR LED, 870nm, T-1 3/4 (5mm) Through Hole package | DS1, DS2, DS3, DS4 | FP-6_544-5258_09-4-MFG | CMP-00030-41223146-1 | 4
UR502DC | Red LED, 80 mW, 30 mA, -25 to 85 degC, 2-Pin THD | DS5, DS6, DS7, DS8 | CGX-UR502DC | CMP-007-00009-2 | 4
TSW-102-07-G-S |  | J1, J2 | SAMTEC_TSW-102-07-G-S | CMP-033-000000-1 | 2
TSW-104-06-L-S |  | J3, P0 | SAMTEC_TSW-104-06-L-S | CMP-009-000000-1 | 2
TSW-105-07-F-S |  | J3_A, J3_B, J4_A, J4_B | SAMTEC_TSW-105-07-F-S | CMP-023-000001-1 | 4
10uH | SMD Inductors 10uH ±20% 0.34A 1.56Ω 0805 | L1 | FP-CB2012-IPC_C | CMP-14484-000302-1 | 1
10uH |  | L3 | WE-TPC_5818 | CMP-0227-00416-3 | 1
MCKPX-G1203A-K4056 | MAGNETIC BUZZER AND TRANSDUCER - More Details | LS1 | FP-MCKPX-G1203A-K4056-MFG | CMP-12433-000001-1 | 1
2.54 |  | P1, P4 | 61300411121 | CMP-1502-01064-3 | 2
2.54 |  | P3 | 61300211121 | CMP-1712-00002-6 | 1
SOT23 | N-Channel Specified PowerTrench(R) MOSFET, 2.5 V, 1.7 A, -55 to 150 degC, 3-Pin SSOT3L, RoHS, Tape and Reel | Q1, Q2, Q4 | FAIR-SSOT3L-3_V | CMP-2000-06249-1 | 3
10K | 10K 0.25W 5% 1206 (3216 Metric) SMD | R2 | RESC1206(3216)_M | CMP-1014-00098-1 | 1
1K | Res Thick Film 0402 1kΩ 1% 0.063W ±100ppm/°C Molded SMD T/R | R3, R10, R13 | FP-RC1005-IPC_A | CMP-13261-004451-1 | 3
6.8K | RES Thick Film, 2.49Ω, 1%, 0.125W, 200ppm/°C, 0805 | R5 | FP-CRCW0805-e3-IPC_B | CMP-02407-004732-1 | 1
10K | RES Thick Film, 2.49Ω, 1%, 0.125W, 200ppm/°C, 0805 | R7 | FP-CRCW0805-e3-IPC_B | CMP-02407-004732-1 | 1
51K | RES Thick Film, 2.49Ω, 1%, 0.125W, 200ppm/°C, 0805 | R8 | FP-CRCW0805-e3-IPC_B | CMP-02407-004732-1 | 1
100k | Res Thick Film 1206 10kΩ 5% 0.25W ±100ppm/°C Molded SMD T/R | R9 | FP-RC3216-IPC_C | CMP-13261-005388-1 | 1
47k |  | R11 | RESC3216X60X45LL10T20 | CMP-2003-02213-1 | 1
0.2 |  | R12 | RESC3216X89X51ML25T25 | CMP-2003-04372-1 | 1
4.7K |  | R16, R17, R18, R19 | RESC3216X60X45LL10T20 | CMP-2003-02213-1 | 4
47k | Chip Resistor, 47 KOhm, +/- 1%, 0.125 W, -55 to 155 degC, 0805 (2012 Metric), RoHS, Tape and Reel | R_BT, R_BT0_1, R_BT0_2, R_BUZZ, R_IR1, R_IR2 | RESC2013X60X35NL10T20 | CMP-1659-00011-4 | 6
10 |  | R_IR3, R_IR4, R_IR5, R_IR6 | RESC2013X50X30NL20T20 | CMP-2001-04915-1 | 4
4.7k | General Puprose Chip Resistor, 4700 Ohm +/- 1%, 0.125 W, -55 to 155 degC, 2-Pin SMD, RoHS, Tape and Reel | R_IR7, R_IR8, R_IR9, R_IR10 | YAGO-RC0805_M | CMP-1568-00001-1 | 4
4mm | Slide Switch, 500 V, -20 to 70 degC, 3-Pin THD, RoHS | SW0 | ESWI-EG1218_V | CMP-1696-00002-1 | 1
STM32F405RGT6 | ARMÂ® CortexÂ®-M4 STM32F4 Microcontroller IC 32-Bit Single-Core 168MHz 1MB (1M x 8) FLASH 64-LQFP (10x10) | U1 | QFP50P1200X1200X160-64N | CMP-031-00006-1 | 1
LM1117IMP-3.3/NOPB | 800mA Low-Dropout Linear Regulator, 4-pin SOT-223, Pb-Free | U2, U6 | DCY0004A_N | CMP-0062-01631-4 | 2
MP2307DN-LF-Z | Buck Switching Regulator IC Positive Adjustable 0.925V 1 Output 3A 8-SOIC (0.154, 3.90mm Width) Exposed Pad | U3 | SOIC127P600X170-9N | MP2307DN-LF-Z | 1
DRV8833PWPR | IC MOTOR DRIVER PAR 16HTSSOP | U5 | FP-PWP0016C-IPC_B | CMP-1529-00004-3 | 1
MT6701CT-STD |  | U_enA, U_enB | SOP-8_L4.9-W3.9-P1.27-LS6.0-BL | MT6701CT-STD | 2
8.000MHZ | CRYSTAL 8.0000MHZ 18PF SMD | Y1 | FP-ABLS-MFG | CMP-27762-009874-1 | 1

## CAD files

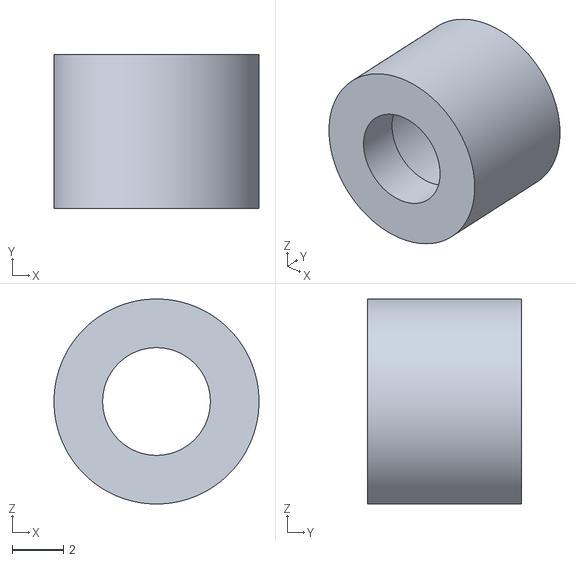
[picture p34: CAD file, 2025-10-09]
hardware/onShape/Final/nam châm.stl
8.00 x 6.00 x 8.00

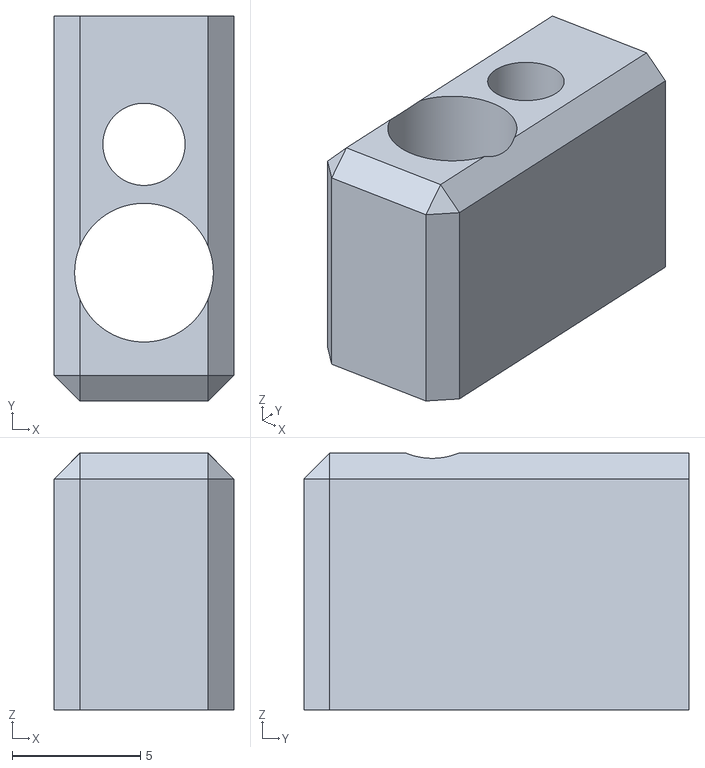
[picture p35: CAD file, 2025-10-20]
hardware/onShape/Ga do ir/Ga do ir - Part 1.stl
7.00 x 15.0 x 10.0

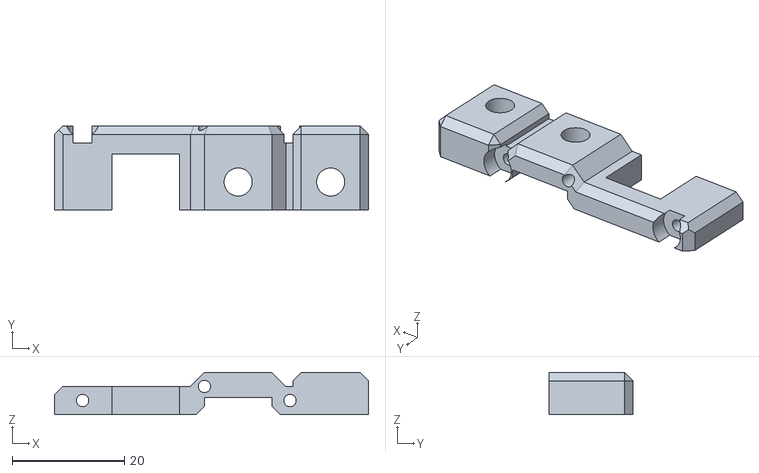
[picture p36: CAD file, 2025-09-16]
hardware/onShape/gá motor (1)/gá motor - Part 1.stl
56.0 x 15.0 x 7.50

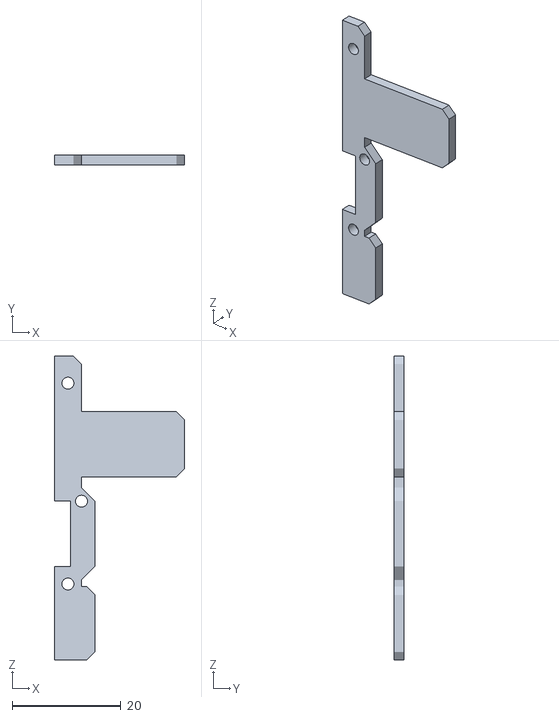
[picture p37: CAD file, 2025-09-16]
hardware/onShape/Final/gá motor - Part 3.stl
24.0 x 1.90 x 56.0

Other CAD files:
hardware/onShape/gá motor - Part 1.step.step.3mf
hardware/onShape/gá motor (1)/gá motor - Part 2.stl
hardware/onShape/gá motor (1)/gá motor - Part 4.stl
hardware/onShape/final/gá motor - Part 2.stl
hardware/onShape/Final/gá motor - Part 4.stl
hardware/onShape/Zalo/zalo/2.2.2.stl
hardware/onShape/Zalo/zalo/2.2.4.stl
hardware/onShape/Zalo/zalo/gá motor - Part 1 (copy).stl
hardware/onShape/Zalo/zalo/gá motor - Part 1.stl
hardware/onShape/Zalo/zalo/gá motor - Part 2 (copy).stl
hardware/onShape/Zalo/zalo/gá motor - Part 2.stl

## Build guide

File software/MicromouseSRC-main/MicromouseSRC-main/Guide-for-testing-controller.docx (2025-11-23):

Guide for testing controller

1. finish implementing the code, don't forget to update the current idea speed for translation and rotation movement every millisecond in systick. You will need to create variable of acceleration/deceleration rate(constant value) to make the mouse accelerate and decelerate in a constant rate. Also, don't forget to accumulate the error for both translation and rotational movement since I put a integral sign on the block diagram in the lecture notes(lecture 3)

2. make the mouse run at a low constant speed on a straight path. It won't go straight as you expected as always since the actual size for 2 wheels are not exactly same. So you need to find the speed difference between left and right wheel in order to compensate the side with less counts to make the mouse go straight with encoder. For example, if right side encoder get 5% less counts than left side wheel every millisecond, then every millisecond, right_speed += left_speed * 5%. However, since the encoder counts are not that large on every millisecond, left_speed*5% will get some value smaller than 1, which will not take any efforts of right wheel, so you need to keep this 5% and accumulate them until it get big enough(equal or greater then 1) then apply on right wheel.

3. Make the mouse accelerate and decelerate for certain distance on at straight path. This is what you need: you need to create a global variable called distanceLeft, and sign the value for it before it starts to run. Ex) if the mouse is going to run for 5 cell distance then stop, you need to overwrite the value for distanceLeft as what encoder counts equals to 5 cells, then keep calling distanceLeft-=((leftSpeed+rightSpeed)/2)

to keep track of the remaining distance.

then you need to utilize equation 2as = Vt^2 - V0^2, by calculating a = abs((Vt^2 - V0^2)/2s) every millisecond to calculate the deceleration rate need in order to reach the target speed within the remaining distance, where parameter "s" is the distanceleft, Vt is the initial speed, V0 is the target speed. IF we want to decelerate to zero speed, then Vt is the current speed, and V0 is the target speed which is zero. Apply them into equation to get the a, which is the deceleration rate needed, compare with the deceleration rate you set, if it is larger than your, it's the time to decelerate, and just simply set your target speedX to zero and mouse will decelerate back to 0 automatically. If the acceleration rate needed is smaller than yours, remain the target speed when you set at the beginning(which is the max speed you want).

4. After test with very high acceleration/speed on the straight path, you will find the mouse gets unstable, now you need to add gyro as feedback to help mouse keep straight since encoder gets noisy at high speed. Before you do this, you need to calibrate gyro as I mentioned in lecture 2, then scale the angular velocity down with certain value as part of the rotational feedback, you need to pay attention of the sign of gyro feedback when you add them with encoder feedback.

5. After you add gyro feedback and make it go straight at high speed, now it's the time for you to add the scaled sensor error as part of the rotational feedback to keep the mouse in center of the cell with the help of both encoder, gyro and IR sensor. Since value for sensor error is significantly larger than any other feedback, you need to scale it down, test and find proper scale, also pay attention with the sign of the sensor error.

6. after you make step 5, you get go test pivot turn with same controller by setting targetSpeedX as 0 and targetSpeedW as a constant, where positive value makes mouse spin to one direction and negative value makes the mouse spins to the opposite way. During pivot turn, you still only use encoder as translational feedback, but you only use either encoder or gyro as the rotational feedback. when you want to turn certain angle, use angle of the gyro as the terminate condition to make the mouse stop spinning at the designated angle. After you finish this, you have all you need to make a basic search other than search algorithm.

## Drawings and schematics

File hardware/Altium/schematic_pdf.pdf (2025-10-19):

# GND1 2

# Power MCU

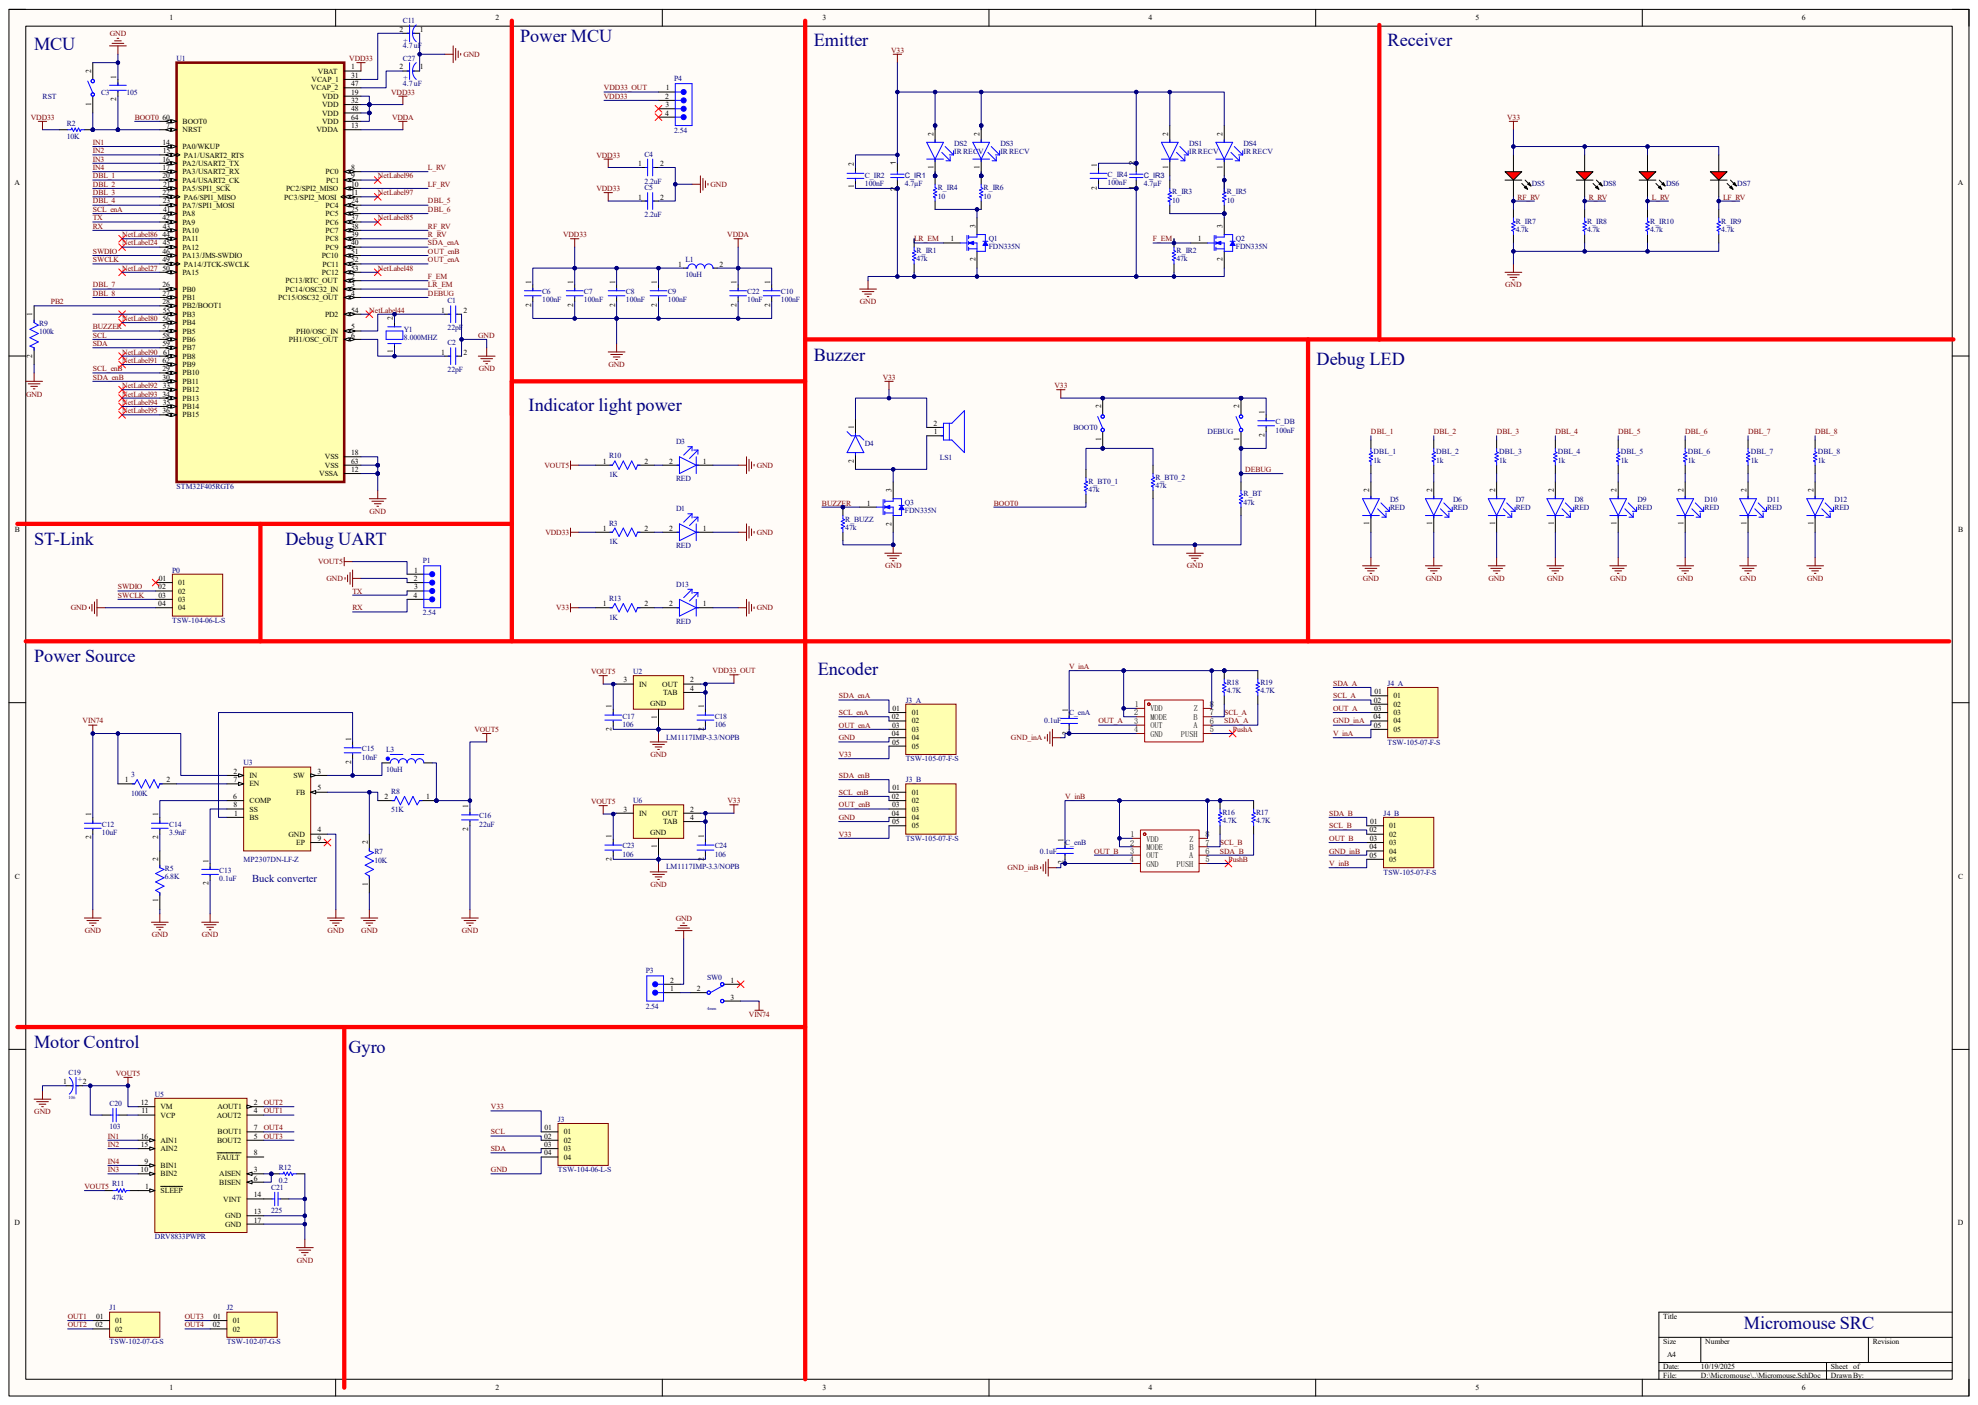
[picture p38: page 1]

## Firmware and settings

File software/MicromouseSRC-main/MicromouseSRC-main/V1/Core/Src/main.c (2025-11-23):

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
/* Includes ------------------------------------------------------------------*/
#include "main.h"

ADC_HandleTypeDef hadc1;
DMA_HandleTypeDef hdma_adc1;

I2C_HandleTypeDef hi2c2;

TIM_HandleTypeDef htim1;
TIM_HandleTypeDef htim2;
TIM_HandleTypeDef htim3;
TIM_HandleTypeDef htim4;

UART_HandleTypeDef huart1;

void SystemClock_Config(void);
static void MX_GPIO_Init(void);
static void MX_DMA_Init(void);
static void MX_TIM1_Init(void);
static void MX_TIM2_Init(void);
static void MX_TIM3_Init(void);
static void MX_ADC1_Init(void);
static void MX_TIM4_Init(void);
static void MX_USART1_UART_Init(void);
static void MX_I2C2_Init(void);
/* USER CODE BEGIN 0 */
//void HAL_GPIO_EXTI_Callback(uint16_t GPIO_Pin) {
//	if(GPIO_Pin == BTN1_Pin) {
//		BTN_STATE1 = 1;
//	}
//	if(GPIO_Pin == BTN2_Pin) {
//		BTN_STATE2 = 1;
//	}
//}
void HAL_TIM_PeriodElapsedCallback(TIM_HandleTypeDef *htim) {

	if (htim == &htim4) {
		read_en_left(&encoder_left);
		read_en_right(&encoder_right);
	}
}

void HAL_ADC_ConvCpltCallback(ADC_HandleTypeDef *hadc) {
	if (hadc->Instance == ADC1) {
		HAL_ADC_Stop_DMA(hadc);  // Dừng ADC
		completeADC = 1;            // Dánh dấu đã hoàn tất
	}
}

void test2() {
	Move_to_middle(40, 180);
	PID_reset(&pid_steering);
	PID_reset(&pid_wall_stable);
	PID_reset(&pid_forward_right);
	PID_reset(&pid_forward_left);
//	delay_ms(5000);
	pushBack(&mouse_state, 0);

	// 10 bước đầu
	for (int i = 0; i < 10; i++) {
		pushBack(&mouse_state, 1);
	}
	// rẽ trái
	pushBack(&mouse_state, 3);
	// đi thẳng 3 steps
	for (int i = 0; i < 3; i++) {
		pushBack(&mouse_state, 1);
	}
	// rẽ trái
	pushBack(&mouse_state, 3);
	// đi thẳng 2 bước
	for (int i = 0; i < 2; i++) {
		pushBack(&mouse_state, 1);
	}

// rẽ phải
	pushBack(&mouse_state, 2);
	// đi 1 bước
	pushBack(&mouse_state, 1);

	// rẽ trái
	pushBack(&mouse_state, 3);
	// đi thẳng 1 bước
	pushBack(&mouse_state, 1);
	// rẽ phải
	pushBack(&mouse_state, 2);
	// đi thẳng 2 bước
	pushBack(&mouse_state, 1);
	for (int i = 0; i < 2; i++) {
		pushBack(&mouse_state, 1);
	}
	// rẽ phải
	pushBack(&mouse_state, 2);
	// đi thẳng 1 bước
	pushBack(&mouse_state, 1);
	// rẽ trái
	pushBack(&mouse_state, 3);
	// đi 1 bước
	pushBack(&mouse_state, 1);
	// rẽ trái
	pushBack(&mouse_state, 3);
	// đi 2 bước
	pushBack(&mouse_state, 1);
	pushBack(&mouse_state, 1);
	// rẽ trái
	pushBack(&mouse_state, 3);

	pushBack(&mouse_state, 1);
	pushBack(&mouse_state, 2);

	pushBack(&mouse_state, 1);
	pushBack(&mouse_state, 2);
	pushBack(&mouse_state, 1);

	//***********
	pushBack(&mouse_state, 2);

	for (int i = 0; i < 2; i++) {
		pushBack(&mouse_state, 1);
	}

	pushBack(&mouse_state, 3);
	pushBack(&mouse_state, 1);
	pushBack(&mouse_state, 3);
	pushBack(&mouse_state, 1);
	pushBack(&mouse_state, 2);
	pushBack(&mouse_state, 1);

	pushBack(&mouse_state, 0);
//	cnt_cell = 4;
	reset_encoder();
	for (int i = 0; i < mouse_state.size; i++) {
//		printf("%d\n\n", CNT_EXT);
		mouse_move();
		mouse_state.index++;
//		if (get(&mouse_state, mouse_state.index) == 2) {
//			encoder_cnt_left += 20;
//			encoder_cnt_right -= 20;
//		}
		calc_extra_cnt();

	}
	freeVector(&mouse_state);
//	Motor_stop();
}

void Solver() {
	Action nextMove = solver();
	switch (nextMove) {
	case FORWARD:
		Move_onecell();
		break;
	case RIGHT:
		delay_ms(400);
		Turn_right90_2();
		delay_ms(200);
		break;
	case LEFT:
		delay_ms(400);
		Turn_left90_2();
		delay_ms(200);
		break;
	case IDLE:
		break;
	}
}

int _write(int fd, char *ptr, int len) {
	HAL_StatusTypeDef hstatus;

	if (fd == 1 || fd == 2) {
		hstatus = HAL_UART_Transmit(&huart1, (uint8_t*) ptr, len,
				HAL_MAX_DELAY);
		if (hstatus == HAL_OK)
			return len;
		else
			return -1;
	}
	return -1;
}

/* USER CODE END 0 */

/**
 * @brief  The application entry point.
 * @retval int
 */
int main(void) {

	/* MCU Configuration--------------------------------------------------------*/

	/* Reset of all peripherals, Initializes the Flash interface and the Systick. */
	HAL_Init();

	/* Configure the system clock */
	SystemClock_Config();

	/* Initialize all configured peripherals */
	MX_GPIO_Init();
	MX_DMA_Init();
	MX_TIM1_Init();
	MX_TIM2_Init();
	MX_TIM3_Init();
	MX_ADC1_Init();
	MX_TIM4_Init();
	MX_USART1_UART_Init();
	MX_I2C2_Init();
	/* USER CODE BEGIN 2 */
//	store_data_memory(0x0801FC10, (uint8_t *) data, sizeof(data));
	HAL_GPIO_WritePin(GPIOC, GPIO_PIN_13, RESET);

	Motor_Init(&motor_right, &htim1, &htim1, TIM_CHANNEL_1, TIM_CHANNEL_2);
	Motor_Init(&motor_left, &htim1, &htim1, TIM_CHANNEL_3, TIM_CHANNEL_4);
	Encoder_Init(&encoder_left, &htim2);
	Encoder_Init(&encoder_right, &htim3);
	HAL_TIM_Base_Start_IT(&htim4);

	Set_Motor_speed(&motor_left, 0);
	Set_Motor_speed(&motor_right, 0);

	PID_init(&pid_forward_left, 1.2, 0.02, 0.9, 0, 0);
	PID_init(&pid_forward_right, 1.2, 0.02, 0.9, 0, 0);
	PID_init(&pid_steering, 8, 0, 3, 0, 0);
	PID_init(&pid_turn_left, 20, 0.02, 2, 0, 0);
	PID_init(&pid_turn_right, 20, 0.02, 2, 0, 0);
	PID_init(&pid_wall_stable, 10, 0, 1.4, 0, 0);
	PID_init(&pid_wall_front_left, 20, 0, 2, 0, 0);
	PID_init(&pid_wall_front_right, 20, 0, 2, 0, 0);

	initVector(&mouse_state, 1000);
//	while (MPU6050_Init(&hi2c2) == 1)
//		;
//	MPU6050_calibration(&hi2c2);
//	angle = 0;
	IR_init(&hadc1);
	ir_calibration();
	wall_calib_offset();

	mode();

	while (IR_LL > 100) {
		read_ir_adc();
//		printf("%f   %f   %f   %f\n", IR_FR_raw, IR_RR_raw, IR_FL_raw, IR_LL_raw);
//		delay_ms(40);
	}
	blink_led(2);
//	Move_onecell();
	test2();

	initialize();

	/* USER CODE END 2 */

	/* Infinite loop */
	/* USER CODE BEGIN WHILE */
//	Move_to_middle(30, 180);
//	PID_reset(&pid_steering);
//	PID_reset(&pid_wall_stable);
//	PID_reset(&pid_forward_right);
//	PID_reset(&pid_forward_left);bb
//	for(int i = 0; i < 10; i ++) {
//		printf("%ld\n", encoder_cnt_left - encoder_cnt_right);
//		blink_led(1);
//	}
//	delay_ms(400);
//	Turn_left90_2();
//	delay_ms(400);
//	Turn_left90_2();
	reset_encoder();
	while (1) {
		read_ir_adc();
		//		Solver();
		delay_ms(40);
//		printf("%d\n", floodFill());
		/* USER CODE END WHILE */

		/* USER CODE BEGIN 3 */
	}
	/* USER CODE END 3 */
}

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


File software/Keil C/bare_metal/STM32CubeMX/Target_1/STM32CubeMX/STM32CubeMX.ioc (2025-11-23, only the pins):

Mcu.UserName=STM32F405RGTx
PA0-WKUP.GPIO_Label=ADC_RF_RV
PA0-WKUP.Signal=ADCx_IN0
PA1.GPIO_Label=ADC_LF_RV
PA1.Signal=ADCx_IN1
PA2.GPIO_Label=ADC_R_RV
PA2.Signal=ADCx_IN2
PA3.GPIO_Label=ADC_L_RV
PA3.Signal=ADCx_IN3
PA4.GPIO_Label=DBL_1
PA4.Signal=GPIO_Output
PA5.GPIO_Label=DBL_2
PA5.Signal=GPIO_Output
PA6.GPIO_Label=DBL_3
PA6.Signal=GPIO_Output
PA7.GPIO_Label=DBL_4
PA7.Signal=GPIO_Output
PB0.GPIO_Label=DBL_7
PB0.Signal=GPIO_Output
PB1.GPIO_Label=DBL_8
PB1.Signal=GPIO_Output
PB12.GPIO_Label=DEBUG_1
PB12.Signal=GPIO_Input
PB13.GPIO_Label=DEBUG_2
PB13.Signal=GPIO_Input
PB14.Signal=TIM1_CH2N
PB15.Signal=TIM1_CH3N
PC0.GPIO_Label=ADC_enA
PC0.Signal=ADCx_IN10
PC1.GPIO_Label=ADC_enB
PC1.Signal=ADCx_IN11
PC10.Signal=UART4_TX
PC11.Signal=UART4_RX
PC4.GPIO_Label=DBL_5
PC4.Signal=GPIO_Output
PC5.GPIO_Label=DBL_6
PC5.Signal=GPIO_Output
PC7.GPIO_Label=PWM_IN4
PC7.Signal=S_TIM3_CH2
PC8.GPIO_Label=PWM_IN3
PC8.Signal=S_TIM3_CH3

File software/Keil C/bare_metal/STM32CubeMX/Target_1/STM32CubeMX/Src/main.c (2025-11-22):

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
/* Includes ------------------------------------------------------------------*/
#include "main.h"
#include <stdio.h>  // Để dùng sprintf
#include <string.h> // Để dùng strlen

/* USER CODE BEGIN PD */
#define ADC_BUFFER_SIZE 50 // number of samples to collect

/* USER CODE END PD */

/* USER CODE BEGIN PV */
uint16_t adc_buffer[ADC_BUFFER_SIZE]; // buffer to hold ADC samples
volatile uint8_t dma_transfer_complete = 0; // flag to indicate DMA transfer completion

// <<< SỬA LỖI (Thêm biến cho Systick) >>>
volatile uint16_t g_latest_avg_val = 0; // Biến "an toàn" để in
volatile uint32_t g_systick_counter = 0; // Bộ đếm cho Systick
/* USER CODE END PV */

/* USER CODE BEGIN PFP */
void My_Clock_Init_HSI(void);
void My_GPIO_Init(void); 
void My_DMA_Init(void);
void My_ADC_Init(void);
void MY_NVIC_Init(void);
void My_UART_GPIO_Init(void);
void My_UART_Init(void);
void UART_SendChar(char c);     
void UART_SendString(char* s);  
void UART_SendNumber(uint16_t num);
void DMA2_Stream0_IRQHandler(void);
void My_SysTick_Init(void); // <<< SỬA LỖI (Thêm prototype) >>>
void My_IR_LED_Init(void);
/* USER CODE END PFP */

/**
  * @brief  The application entry point.
  * @retval int
  */
int main(void)
{
  /* USER CODE BEGIN 1 */
  // <<< SỬA LỖI (Gọi Clock NGAY LẬP TỨC) >>>
  My_Clock_Init_HSI();
  /* USER CODE END 1 */

  /* MCU Configuration--------------------------------------------------------*/

  /* Initialize all configured peripherals */
  /* USER CODE BEGIN 2 */
  //My_Clock_Init_HSI(); // <<< SỬA LỖI (Đã di chuyển lên USER CODE 1) >>>
  My_GPIO_Init();
  My_DMA_Init();
  My_ADC_Init();
  MY_NVIC_Init();
  My_UART_GPIO_Init();
  My_UART_Init();
  My_SysTick_Init(); // <<< SỬA LỖI (Gọi hàm Init Systick) >>>
  My_IR_LED_Init();
  // Start ADC Conversion
  ADC1->CR2 |= ADC_CR2_SWSTART;
  UART_SendString("Hello!\r\n");
  UART_SendString("Testing...\r\n");
  /* USER CODE END 2 */

  /* Infinite loop */
  /* USER CODE BEGIN WHILE */
  while (1)
  {
    /* USER CODE END WHILE */

    /* USER CODE BEGIN 3 */
    // Tắt LED (Ghi 1)
    //GPIOC->BSRR = GPIO_BSRR_BR_13;
    // Gửi 1 (3.3V) tới PC13 để BẬT N-MOSFET
    GPIOC->BSRR = GPIO_BSRR_BS_13; //BS mean Set, BR mean Reset
    // <<< SỬA LỖI (Tách biệt logic tính toán và logic in) >>>
    if (dma_transfer_complete == 1)
    {
      // 1. XÓA CỜ NGAY LẬP TỨC
      dma_transfer_complete = 0; 

      // 2. Chỉ tính toán và cập nhật biến "an toàn"
      // (Không cần copy buffer, vì chúng ta chỉ cập nhật 1 biến)
      uint32_t sum = 0;
      for(int i=0; i < ADC_BUFFER_SIZE; i++)
      {
        sum += adc_buffer[i];
      }
      
      // 3. Cập nhật biến
      // Ngắt SysTick sẽ tự động lấy biến này để in
      g_latest_avg_val = sum / ADC_BUFFER_SIZE;
      
      // 4. TUYỆT ĐỐI KHÔNG GỌI UART_SendNumber() TẠI ĐÂY
    }
  }
  /* USER CODE END 3 */
}

/* USER CODE BEGIN 4 */

/**
  * @brief Cấu hình SysTick timer 1ms (Giả định HCLK 168MHz)
  * @retval None
  */
// <<< SỬA LỖI (Thêm hàm Init Systick) >>>
void My_SysTick_Init(void)
{
  // Clock của bạn là 168MHz (từ hàm My_Clock_Init_HSI)
  // 168.000.000 / 1000 (cho 1ms) = 168000
  SysTick_Config(168000); 
}

/**
  * @brief Hàm xử lý ngắt SysTick (Tên hàm là bắt buộc)
  * @retval None
  */
// <<< SỬA LỖI (Thêm hàm Handler Systick) >>>
void SysTick_Handler(void)
{
  g_systick_counter++; // Tăng bộ đếm mỗi 1ms

  // In 10 lần 1 giây (mỗi 100ms)
  if (g_systick_counter >= 100)
  {
    g_systick_counter = 0; // Reset bộ đếm
    
    // In giá trị trung bình "an toàn"
    UART_SendNumber(g_latest_avg_val);
  }
}

/**
  * @brief Cấu hình PC2 
  * @retval None
  */
void My_GPIO_Init(void)
{
  // 1. Enable GPIO clock
  RCC->AHB1ENR |= RCC_AHB1ENR_GPIOCEN;

  // 2. Configure PC2 as an analog input
  GPIOC->MODER |= GPIO_MODER_MODE2;

  // 3. Disable pull-up/pull-down resistors for PC2
  GPIOC->PUPDR &= ~GPIO_PUPDR_PUPD2; 
}

/**
  * @brief Cấu hình DMA2 Stream 0 cho ADC1
  * @retval None
  */
void My_DMA_Init(void)
{
  // 1. Enable DMA2 clock
  RCC->AHB1ENR |= RCC_AHB1ENR_DMA2EN;

  // 2. Configure DMA2 Stream 0 for ADC1
  DMA2_Stream0->CR &= ~DMA_SxCR_EN; 
  while (DMA2_Stream0->CR & DMA_SxCR_EN);

  // 3. SET CHANNEL 0 FOR STREAM 0
  DMA2_Stream0->CR &= ~DMA_SxCR_CHSEL; 

  // 4. SET ADDRESS OF PERIPHERAL (ADC1 DATA REGISTER)
  DMA2_Stream0->PAR = (uint32_t)&ADC1->DR;

  // 5. SET ADDRESS OF MEMORY (adc_buffer)
  DMA2_Stream0->M0AR = (uint32_t)adc_buffer;

  // 6. SET NUMBER OF DATA ITEMS TO TRANSFER
  DMA2_Stream0->NDTR = ADC_BUFFER_SIZE;

  // 7. CONFIGURE CONTROL REGISTER
  DMA2_Stream0->CR |= DMA_SxCR_PL_1; 
  DMA2_Stream0->CR |= DMA_SxCR_MSIZE_0; 
  DMA2_Stream0->CR |= DMA_SxCR_PSIZE_0; 
  DMA2_Stream0->CR |= DMA_SxCR_MINC; 
  DMA2_Stream0->CR |= DMA_SxCR_CIRC;    

  DMA2_Stream0->CR |= DMA_SxCR_TCIE;
  // 8. ENABLE DMA STREAM
  DMA2_Stream0->CR |= DMA_SxCR_EN;
}

void My_ADC_Init(void)
{
  // 1. Enable ADC1 clock
  RCC->APB2ENR |= RCC_APB2ENR_ADC1EN; // set bit adc1 lên 1 

  // 2. Configure ADC1 ( CR1 )
  ADC1->CR1 |= ADC_CR1_SCAN; // adc sẽ thực hiện scan nhiều kênh (nếu có)

  // 3. CONFIGURE ADC1 ( CR2 )
  ADC1->CR2 |= ADC_CR2_CONT; // adc sẽ thực hiện liên tục, cr2 register
  ADC1->CR2 |= ADC_CR2_DMA;  // enable dma for adc
  ADC1->CR2 |= ADC_CR2_DDS;  // dma sẽ request liên tục, dds is dma disable selection
  
  // 4. CONFIGURE ADC1 REGULAR SEQUENCE ( SQR3 )
  ADC1->SQR1 &= ~ADC_SQR1_L; // 0B0000 = 1 CONVERSION
  // (Chúng ta chỉ đọc 1 kênh duy nhất)
  // sqr1 register is for length of sequence

  // 5. CONFIGURE SEQUANCE REGISTER 3 ( SQR3 )
  ADC1->SQR3 = (12 << ADC_SQR3_SQ1_Pos); // 

  // 6. CONFIGURE SAMPLING TIME ( SMPR1 )
  //ADC1->SMPR1 |= (0b110 << ADC_SMPR1_SMP12_Pos); 
  ADC1->SMPR1 |= (0b111 << ADC_SMPR1_SMP12_Pos);
  // 7. ENABLE ADC1
  ADC1->CR2 |= ADC_CR2_ADON;

  // 8.  WAIT FOR ADC1 TO STABILIZE
  for (volatile uint32_t i = 0; i < 10000; i++);
}

void MY_NVIC_Init(void)
{
  // ENABLE DMA2 STREAM0 INTERRUPT IN NVIC
  NVIC_SetPriority(DMA2_Stream0_IRQn, 1);
  NVIC_EnableIRQ(DMA2_Stream0_IRQn);
}

void DMA2_Stream0_IRQHandler(void)
{
  // 1. check TRANSFER COMPLETE FLAG
  if (DMA2->LISR & DMA_LISR_TCIF0)
  {
    // CLEAR THE TRANSFER COMPLETE FLAG
    DMA2->LIFCR = DMA_LIFCR_CTCIF0;

    // SET THE TRANSFER COMPLETE FLAG
    dma_transfer_complete = 1;
  }
}

void My_UART_GPIO_Init(void)
{
  // 1. Cấp clock cho GPIOA (chứa PA9)
  RCC->AHB1ENR |= RCC_AHB1ENR_GPIOAEN;

  // 2. Chuyển PA9 sang chế độ Alternate Function (AF)
  GPIOA->MODER &= ~GPIO_MODER_MODE9_0;
  GPIOA->MODER |= GPIO_MODER_MODE9_1;

  // 3. Đặt tốc độ (Speed) cho chân (ví dụ: High Speed)
  GPIOA->OSPEEDR |= GPIO_OSPEEDR_OSPEED9; 

  // 4. Cấu hình Alternate Function là AF7 (cho USART1)
  GPIOA->AFR[1] &= ~GPIO_AFRH_AFSEL9; 
  GPIOA->AFR[1] |= (7 << GPIO_AFRH_AFSEL9_Pos); 
}
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

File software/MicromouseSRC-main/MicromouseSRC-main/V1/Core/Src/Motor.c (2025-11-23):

/*
 * Motor.c
 *
 *  Created on: Feb 28, 2025
 *      Author: kinhz
 */

#include "Motor.h"

Motor motor_left;
Motor motor_right;

uint32_t prev_time_pid_forward = 0;
uint32_t prev_time_pid_rotation = 0;
int32_t debug_pwm = 0;

uint8_t MOUSE_STATE = 0;

void Motor_Init(Motor *motor, TIM_HandleTypeDef *tim1, TIM_HandleTypeDef *tim2,
		uint16_t channel1, uint16_t channel2) {
	motor->M_TIM1 = tim1;
	motor->M_TIM2 = tim2;
	motor->m_channel1 = channel1;
	motor->m_channel2 = channel2;

	HAL_TIM_PWM_Start(tim1, channel1);
	HAL_TIM_PWM_Start(tim2, channel2);
}

void Set_Motor_speed(Motor *motor, int16_t speed) {
	if (speed > 0) {
		__HAL_TIM_SET_COMPARE(motor->M_TIM1, motor->m_channel1, 0);
		__HAL_TIM_SET_COMPARE(motor->M_TIM2, motor->m_channel2, speed);
	} else {
		__HAL_TIM_SET_COMPARE(motor->M_TIM1, motor->m_channel1, -speed);
		__HAL_TIM_SET_COMPARE(motor->M_TIM2, motor->m_channel2, 0);
	}
}

void Move_to_middle(float distance, float speed) { // distance in cm ,speed in mm/s
//	int16_t count = 0;
	reset_en();

	speed = mm_to_cnt(speed);
	distance = mm_to_cnt(distance);
	prev_time_pid_forward = Millis;
	prev_time_pid_rotation = Millis;
	read_ir_adc();
//	uint32_t curt = Micros;
	PID_reset(&pid_steering);
	PID_reset(&pid_wall_stable);
	PID_reset(&pid_forward_right);
	PID_reset(&pid_forward_left);
	while ((distance > encoder_cnt_left) || (distance > encoder_cnt_right)) {
		int16_t left_pwm = PID_calc(&pid_forward_left, speed, speed_left,
				Millis - prev_time_pid_forward);
		int16_t right_pwm = PID_calc(&pid_forward_right, speed, speed_right,
				Millis - prev_time_pid_forward);
		prev_time_pid_forward = Millis;
		int16_t error_steering = PID_calc(&pid_steering, 0,
				encoder_cnt_left - encoder_cnt_right,
				Millis - prev_time_pid_rotation);
		prev_time_pid_rotation = Millis;
		left_pwm += error_steering;
		right_pwm += -error_steering;

		if (left_pwm > 10000)
			left_pwm = 10000;
		if (left_pwm < 0)
			left_pwm = 0;
		if (right_pwm > 10000)
			right_pwm = 10000;
		if (right_pwm < 0)
			right_pwm = 0;

		Set_Motor_speed(&motor_left, left_pwm);
		Set_Motor_speed(&motor_right, right_pwm);

//		elapseMillis(1000, curt);
//		curt = Micros;

		delay_ms(1);
//		read_ir_adc();
	}
	Motor_stop();
}

void Turn_left90() {
	angle = 0;
	uint32_t prev_time = micros();
	uint32_t curt = Millis;
	PID_reset(&pid_forward_right);
	PID_reset(&pid_forward_left);
	float target_angle = 13 + cnt_to_omega(encoder_cnt_left, encoder_cnt_right);
	while (fabs(target_angle - angle) > 4) {
		MPU6050_getAngle(MPU6050.I2Cx, micros() - prev_time);
		printf("%f\n\n", angle);
		int16_t pwm_target = 120 * (target_angle - angle);
		int16_t left_pwm = PID_calc(&pid_forward_left, -pwm_target, speed_left,
				micros() - prev_time);
		int16_t right_pwm = PID_calc(&pid_forward_right, pwm_target,
				speed_right, micros() - prev_time);
		prev_time = micros();
		if (left_pwm < -1400)
			left_pwm = -1400;
		if (right_pwm > 1400)
			right_pwm = 1400;
		Set_Motor_speed(&motor_left, left_pwm);
		Set_Motor_speed(&motor_right, right_pwm);

//		elapseMillis(2, curt);
//		curt = Millis;
		delay_ms(2);
	}
//	reset_en();
//	printf("%f\n", angle);
	Motor_stop();
//	delay_ms(20);
}

void Turn_right90() {
	angle = 0;

	reset_en();
	uint32_t prev_time = micros();
//	uint32_t prev_time_check = Millis;
	uint32_t curt = Millis;
	PID_reset(&pid_forward_right);
	PID_reset(&pid_forward_left);
	while (fabs(80 + angle - cnt_to_omega(encoder_cnt_left, encoder_cnt_right))
			> 4) {
		MPU6050_getAngle(MPU6050.I2Cx, micros() - prev_time);

		int16_t pwm_target = 25 * (80 + angle);
		int16_t left_pwm = PID_calc(&pid_forward_left, pwm_target, speed_left,
				micros() - prev_time);
		int16_t right_pwm = PID_calc(&pid_forward_right, -pwm_target,
				speed_right, micros() - prev_time);
		prev_time = micros();
		if (left_pwm > 1600)
			left_pwm = 1600;
		if (right_pwm < -1600)
			right_pwm = -1600;
		Set_Motor_speed(&motor_left, left_pwm);
		Set_Motor_speed(&motor_right, right_pwm);

		elapseMillis(2, curt);
		curt = Millis;
	}
//	reset_en();
	Motor_stop();
//	delay_ms(20);
//	printf("%f\n", angle);
}

void Motor_stop() {
	Set_Motor_speed(&motor_right, 0);
	Set_Motor_speed(&motor_left, 0);
}

void Adjuster() {
//	int curt = Millis;
	int32_t curt = micros();
	while ((fabs(IR_FL_raw - WALL_FL) > 200)
			|| (fabs(WALL_FR - IR_FR_raw) > 200)) {
		read_ir_adc();
		Set_Motor_speed(&motor_right, 2000);
		Set_Motor_speed(&motor_left, 2000);
		elapseMicros(1000, curt);
	}
	Motor_stop();
}

void Move_onecell() {
//	reset_en();
//	calc_extra_cnt();

//	if (floodFill() != FORWARD) state = 0;
	if (get(&mouse_state, mouse_state.index - 1) != 1) {
		PID_reset(&pid_steering);
		PID_reset(&pid_wall_stable);
		PID_reset(&pid_forward_right);
		PID_reset(&pid_forward_left);
	}
	uint32_t prev_time = micros();
	uint32_t distance = mm_to_cnt(onecell);
	int16_t right_pwm;
	int16_t left_pwm;
	while ((distance > encoder_cnt_left) || (distance > encoder_cnt_right)) {
//			&& ((IR_FL < WALL_FL) || (IR_FR < WALL_FR))) {
		update_speed(micros() - prev_time, check_state());
		left_pwm = PID_calc(&pid_forward_left, mm_to_cnt(_SPEED), speed_left,
				micros() - prev_time);
//		debug_pid ++;
		right_pwm = PID_calc(&pid_forward_right, mm_to_cnt(_SPEED), speed_right,
				micros() - prev_time);
		int16_t error_steering = PID_calc(&pid_steering, 0,
				encoder_cnt_left - encoder_cnt_right, micros() - prev_time);
		int16_t error_wall = PID_calc(&pid_wall_stable, 0,
				wall_side_calibration(), micros() - prev_time);
		prev_time = micros();
		error_wall *= (speed_left + speed_right) / mm_to_cnt(2 * SPEED_MAX);
		error_wall = 0;
		left_pwm += error_steering - error_wall;
		right_pwm += -error_steering + error_wall;

		if (left_pwm > 10000)
			left_pwm = 10000;
		if (left_pwm < 0)
			left_pwm = 0;
		if (right_pwm > 10000)
			right_pwm = 10000;
		if (right_pwm < 0)
			right_pwm = 0;

		Set_Motor_speed(&motor_left, left_pwm);
		Set_Motor_speed(&motor_right, right_pwm);
		delay_ms(1);
	}
}

void Turn_left90_2() {
	PREV_TURNSPEED = 0;
	reset_en();
	PID_reset(&pid_forward_right);
	PID_reset(&pid_forward_left);
	PID_reset(&pid_steering);
	read_ir_adc();
	int8_t back_t = 0;
	if(IR_LL_raw > WALL_L - 200) {
		back_t = 1;
	}
	float angle_target = mm_to_cnt(perimeter) / 4 - 50 + CNT_EXT;
	int16_t left_pwm = 0, right_pwm = 0;
	int8_t state = 1;
	uint32_t prev_time = micros();
	while (-angle_target < encoder_cnt_left) {
		update_turnspeed(micros() - prev_time, state);
		left_pwm = PID_calc(&pid_forward_left, -TURN_SPEED,
				speed_left, micros() - prev_time);
		right_pwm = PID_calc(&pid_forward_right, TURN_SPEED,
				speed_right, micros() - prev_time);
		prev_time = micros();
		if (angle_target + encoder_cnt_left < 40)
			state = 0;



		Set_Motor_speed(&motor_left, left_pwm);
		Set_Motor_speed(&motor_right, right_pwm);
		delay_ms(2);
	}
	Motor_stop();
	if(back_t == 1)
		Back();
	Move_to_middle(40, 180);
	reset_encoder();
}
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

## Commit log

2025-08-03 schematic and pcb init
    [PCB1.PcbDoc, Sheet1.SchDoc]
2025-08-06 xóa mms1
    [PCB1.PcbDoc, Sheet1.SchDoc, mmsVersion1.PrjPcb]
2025-08-06 vẽ nguồn
    [Sheet1.SchDoc]
2025-08-06 hoàn thành nguồn 5v, 3v3
    [Sheet1.SchDoc]
2025-08-09 đổi tên điện trở, k ảnh hưởng
2025-08-12 update onShape
    [n20_motor_mounting_bracket.stl]
2025-08-12 update tối ngày 12/8
2025-08-12 update nhỏ
2025-08-17 add encoder
    [Encoder.PcbDoc, Encoder.SchDoc, PCB1.PcbDoc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]
2025-08-17 fix sche encoder
    [Encoder.PcbDoc, Encoder.PrjPcb, Encoder.SchDoc]
2025-08-17 add resistor
2025-08-17 change st-link pin
    [Sheet1.SchDoc]
2025-08-17 add IR
    [Sheet1.SchDoc]
2025-08-17 change gyro schematic
    [Sheet1.SchDoc]
2025-08-17 add thư viện
    [banh_rang_noi_giua.stl]
2025-08-24 update schematic
    [Sheet1.SchDoc]
2025-08-27 chỉnh sửa lại biến trở emmiter
    [PCB1.PcbDoc, Sheet1.SchDoc]
2025-08-27 update debug button
    [Sheet1.SchDoc]
2025-08-31 đi layout pcb
2025-08-31 update pcb
2025-09-01 đổi encoder sang thư mục encoder
    [Encoder.PrjPcb, Micromouse.SchDoc, Micromouse_PCB.PcbDoc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]
2025-09-01 update pcb 9/1 10:18
2025-09-03 prototype 1
    [MT6701CT-STD1_MT6701CT-STD.schdoc, Micromouse.SchDoc, Micromouse_PCB.PcbDoc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]
2025-09-06 chỉnh chỉnh tí
2025-09-06 config folder
    [Encoder.PrjPcb, MT6701CT-STD1_MT6701CT-STD.schdoc, Micromouse.SchDoc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]
2025-09-08 update 3d
    [PCB 3D model - Part 1.stl, bánh xe trục 1.5mm - Part 1 - Copy.stl, bánh xe trục 1.5mm - Part 1.stl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]
2025-09-08 update pcb and add 3d part
    [Circle - Part 1.stl, Circle - Part 2.stl, Circle - Part 3.stl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]
2025-09-16 gerbers file init
    [2.2.1.stl, 2.2.2.stl, 2.2.3.stl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]
2025-09-16 gen gerber
    [Micromouse_PCB.GBL, Micromouse_PCB.GBO, Micromouse_PCB.GBP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]
2025-09-18 final pcb
    [Micromouse_PCB.GM1]
2025-09-19 BOM init
    [BOM.xlsx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]
2025-10-09 update final for hardware
    [2.2.1.stl, 2.2.2.stl, 2.2.3.stl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]
2025-10-09 final update for hardware
    [Encoder.PrjPcb, MT6701CT-STD1_MT6701CT-STD.schdoc, SOP-8_L4.9-W3.9-P1.27-LS6.0-BL.PcbLib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]
2025-10-19 chematic pdf
    [Micromouse.SchDoc]
2025-10-20 add ga do ir
    [Ga do ir - Part 1 - Copy (2).stl, Ga do ir - Part 1 - Copy (3).stl, Ga do ir - Part 1 - Copy.stl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]
2025-11-22 maka a copy
    [BOM.xlsx, Micromouse.SchDoc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]
2025-11-23 update uet code
    [Trapezoidal-Curve-Turn-Profile-Generator.xlsx, mmsVersion1.PrjPcb]
2025-11-23 update pcb 1_2
2025-12-19 update code
    [Micromouse.SchDoc, Micromouse_PCB.PcbDoc]
2025-12-30 new branch
    [Micromouse_1_2.PcbDoc]
2025-12-30 thay diode
    [Micromouse_1_2.SchDoc]
2025-12-31 fix power mcu
    [Micromouse_1_2.PcbDoc, Micromouse_1_2.SchDoc]
2026-01-01 thay doi quartz crystal
    [Micromouse_1_2.PcbDoc, Micromouse_1_2.SchDoc]
2026-01-11 update pcb layout
    [Micromouse_1_2.PcbDoc, Micromouse_1_2.SchDoc]
2026-01-13 update schematic
    dây gnd không nối vì đổ polygon gnd
    [Micromouse_1_2.PcbDoc, Micromouse_1_2.SchDoc]

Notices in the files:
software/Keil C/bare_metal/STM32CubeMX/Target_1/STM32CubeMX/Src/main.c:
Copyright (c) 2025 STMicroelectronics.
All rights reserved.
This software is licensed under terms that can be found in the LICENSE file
